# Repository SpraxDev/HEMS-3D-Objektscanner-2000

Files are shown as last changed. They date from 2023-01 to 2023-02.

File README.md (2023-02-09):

# 3D-Objektscanner 2000
Im Rahmen eines Lernfeldes in der Berufsschule haben wir ([@Yannik-Roesser](https://github.com/Yannik-Roesser) und [@SpraxDev](https://github.com/SpraxDev)) den 3D-Objektscanner 2000 entwickelt.

Im Grunde besteht dieser aus einem Drehteller, auf dem sich ein Objekt befindet – Ein *ToF Sensor* misst die Distanz zum Objekt-Messpunkt und speichert diesen ab.

Der Drehteller dreht sich, wodurch wir eine 360°-Ansicht des Objekts erhalten; Der *ToF Sensor* kann in der Höhe verstellt werden, wodurch wir nun über das gesamte Objekt hinweg messen können.

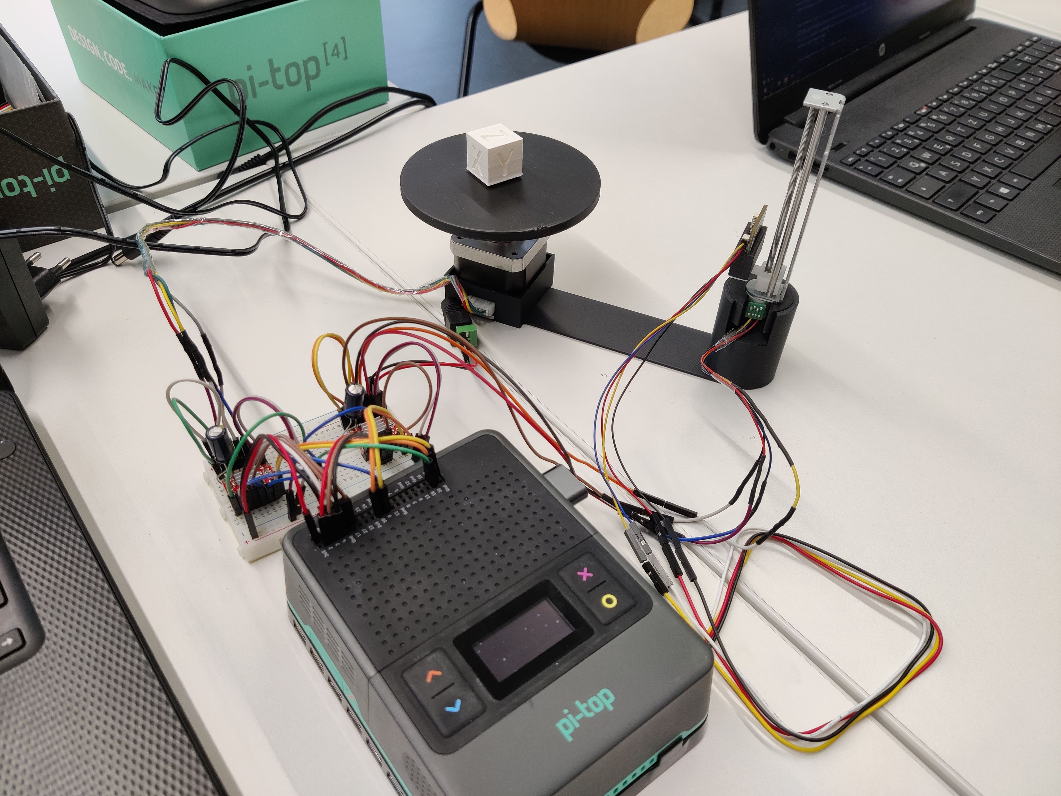
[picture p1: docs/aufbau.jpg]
Bild des Aufbaus mit Raspberry Pi, Drehteller und Distanzsensor

*(Weitere Bilder in [docs/](./docs/))*

## Projektanforderungen
Im Grundlegenden sollten wir folgende Anforderungen erfüllen:
* Verwendung von mindestens vier unterschiedlichen Sensoren oder Aktoren
  * 1x Stepper-Motor (Drehteller)
  * 1x Stepper-Motor mit Linearschlitten (Auf- und Abwärtsbewegung; Für den *ToF Sensor*)
  * 1x ToF Sensor
  * Webinterface (Ein- und Ausgabe; Rendering 3D Modell; Download als STL-Datei)
  * REST-API
* Trennung von Erfassung und Ausgabe der Sensordaten (2 verschiedene Geräte)
  * Erfassung: Python-Script
  * Ausgabe: Webinterface
* Sensorwerte und Eingaben müssen für mindestens 30 Tage gespeichert werden
  * PostgreSQL-Datenbank (Speicherdauer unbegrenzt)
* Fehleingaben des Nutzers müssen entsprechend behandelt werden
  * Validierung der Eingaben
  * Fehlermeldungen (z.B. bei Verbindungsproblemen)
* Klar definiertes Anwendungsgebiet
  * Videospiel-Prototyp günstiger und einfacher herstellen
  * Marketing-Materialien (z.B. für die Produktpräsentation)
  * 3D-Druck (z.B. als Hilfe, wenn ein Objekt als CAD file design werden muss)
  * ...

## Projektstruktur
Das Projekt besteht aus mehrere Software-Komponenten:
* Webinterface-Frontend
* Webinterface-Backend (Webserver + REST-API)
* Python-Script
* FreeCAD
  * Enthält FreeCAD-Projekte, mit Halterungen für die Hardware (zum selber Drucken)
  * Je nach 3D-Druck sind die Maße der Halterungen unter Umständen 1 bis 2 mm zu klein

Funktionen und Aufgaben der Komponenten:
* Das Frontend muss einmalig gebaut werden und kann deployed werden oder vom Backend ausgeliefert werden.
* Das Backend startet einen HTTP-Server, der die REST-API bereitstellt und optional das Frontend ausliefert.
  * Das Backend kann auch auf einem anderen Server laufen, als das Frontend
* Das Python-Script wird auf dem Raspberry Pi ausgeführt, der die meisten Sensoren und Aktoren steuert
  * Das Python-Script kann auch auf einem anderen Server laufen, als das Backend

Die Daten werden in einer PostgreSQL-Datenbank gespeichert.

## Installation
Frontend und Backend benötigen Node.js (getestet mit Version 18) und npm (wird in der Regel mit Node.js mitgeliefert) als package manager.
Für das Python-Skript wird Python 3 benötigt und `pip` als package manager.

### Webinterface-Frontend
1. Im Frontendordner `npm ci` ausführen, um alle notwendigen Pakete zu installieren
2. `npm run build` ausführen, um das Frontend zu bauen
    * Nach der ersten Ausführung, generiert sich eine `config.json` im `config/`-Ordner,
      die angepasst werden kann
3. Das fertige Frontend findet sich im neuen `dist/`-Ordner – Dieses kann (optional) manuell auf ein anderes System deployed werden

### Webinterface-Backend
1. Im Backendordner `npm ci` ausführen, um alle notwendigen Pakete zu installieren
2. `npm run build` ausführen, um das Backend zu bauen
3. Das fertige Backend findet sich im neuen `dist/`-Ordner – Die (production) Abhängigkeiten in `node_modules/` werden zur Ausführung benötigt
4. Zum Starten `npm run start` ausführen
    * Es generiert sich eine `config.json` im `config/`-Ordner, die angepasst werden muss
    * Wurde das Frontend vorab gebaut und die Projekt-Ordnerstruktur nicht verändert, wird dieses
      automatisch gefunden und ausgeliefert

### Python-Script und Hardware
1. Die Hardware, wie in `Verkabelung.fzz` beschrieben, anschließen
2. Die Hardware mit den GPIO-Pins des Raspberry Pi verbinden
    * *ToF Sensor* an den I2C-Bus anschließen
    * Die Motor-Driver-Boards an die entsprechenden Pins aus `scanner-script/scanner_controller.py` (ca. ab Zeile 109 bei `GPIO_motorTeller` und `GPIO_motorVert`)
3. Im Python-Script-Ordner `pip3 install -r requirements.txt` ausführen, um alle notwendigen Pakete zu installieren
    * Es empfiehlt sich vorab ein virtuelles Python-Environment anzulegen
    * Unter Umständen muss `pip` anstelle von `pip3` verwendet werden
4. Skript bei Bedarf konfigurieren
    * `postgres.py` anpassen, um die Datenbankverbindung zu konfigurieren
    * `DISTANCE_BETWEEN_SENSOR_AND_TURN_TABLE_CENTER_MM` in `scanner_controller.py` anpassen, um die Entfernung zwischen dem ToF-Sensor und dem Mittelpunkt des Teller zu konfigurieren
4. `python3 scanner_controller.py` ausführen, um das Script zu starten
    * Unter Umständen muss `python` anstelle von `python3` verwendet werden
5. Das Script wartet nun auf einen Startbefehl über die REST-API

### PostgreSQL Datenbank
Die `/database.sql` enthält die Datenbankstruktur und muss einmalig in die Datenbank eingespielt werden.
Es enthält keine OWNER-Informationen, da diese je nach Umgebung variieren können.

## Unsere Einkaufsliste
Dies sind die Teile, die wir im Rahmen der Projekt-Konzeption verwendet haben.
Ein Breadboard und Kabel sind ebenfalls Notwendig – Die 2 Raspberry Pis haben wir ebenfalls nicht aufgelistet, da diese als Teil der Aufgabenstellung bereits vorhanden waren.

* [Steppermotor mit Linearschlitten](https://smile.amazon.de/dp/B07H4M3KW2/)
  * Hierran befestigen wir unseren *ToF Sensor*
* [NEMA17-04](https://www.reichelt.de/schrittmotor-nema-17-1-8-1-5-a-3-3-v-nema17-04-p269223.html)
  * Nutzen wir für unseren Drehteller (lieber einen stärkeren Motor nehmen, da wir den Teller auch mit Gewicht bewegen wollen)
* 2x [A4988 Schrittmotor-Treiber-Modul](https://www.az-delivery.de/products/a4988-schrittmotor-modul)
  * Damit können wir die beiden Motoren ansteuern
  * [Das Video könnte hilfreich sein](https://www.youtube.com/watch?v=_5H7ibWQgXo)
* [Steckernetzteil 12V 2A](https://www.reichelt.de/steckernetzteil-24-w-12-v-2-a-hnp-24-120l6-p177030.html)
  * Damit können wir den NEMA17-04 bzw. das Treibermodul mit Strom versorgen
* [Kupplung, Ø außen: 5,5 mm, Ø innen: 2,1 mm (DELOCK 65421)](https://www.reichelt.de/kupplung-aussen-5-5-mm-innen-2-1-mm-delock-65421-p127462.html)
  * Darüber verbinden wir das Netzteil mit dem Treibermodul
  * *Hätte auch einfach abgeschnitten und 2 Steckverbindungen draufgelötet, aber lassen wir das beim Schulprojekt mal lieber*
* [Adafruit VL6180X Time of Flight Micro-LIDAR Distance Sensor](https://www.adafruit.com/product/3316)
  * Damit messen wir die Distanz zum Objekt, dass auf dem Drehteller liegt
* 2x [100µF Capacitor (ca. 70 V)](https://www.reichelt.de/elko-radial-100-uf-63-v-105-c-low-esr-aec-q200-rad-fc-100-63-p84621.html)
  * Kommt zur externen Stromversorgung des Motors (möglichst nah am Driver-Board)
    * Details gibts im [Datasheet](https://cdn.shopify.com/s/files/1/1509/1638/files/A4988_Stepper_Motor_Driver_Datenblatt_AZ-Delivery_Vertriebs_GmbH.pdf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)
  * Weniger als 70 V ist sicherlich auch okay, aber keinesfalls unter 40 V würde ich sagen

## Lizenz
Das Projekt ist grundsätzlich unter der MIT-Lizenz veröffentlicht.

Das verwendete Logo im Frontend ist von DinosoftLabs auf Flaticon, lizensiert unter der [Flaticon license](https://www.freepikcompany.com/legal).

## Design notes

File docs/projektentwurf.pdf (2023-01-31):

## Lernfeld 7:

Cyber-physische Systeme ergänzen | Kooperation von Friedrich-List-Schule
| und Heinrich-Emanuel-Merck-Schule
Teammitglieder: Christian Koop, Yannik | in der Ausbildung der IT-Berufe

## Rößer

## Konzept zu [3D-Objektscanner 2000]

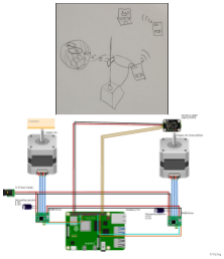
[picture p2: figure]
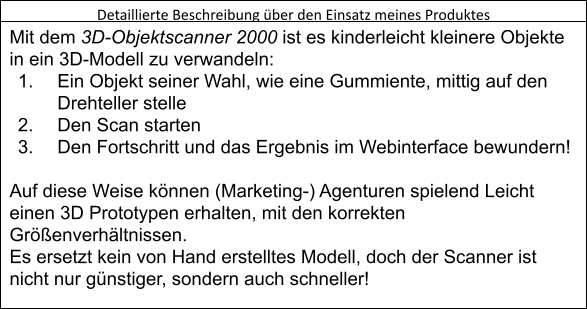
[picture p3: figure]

## Teammitglieder: Christian Koop, Yannik in der Ausbildung der IT-Berufe Rößer

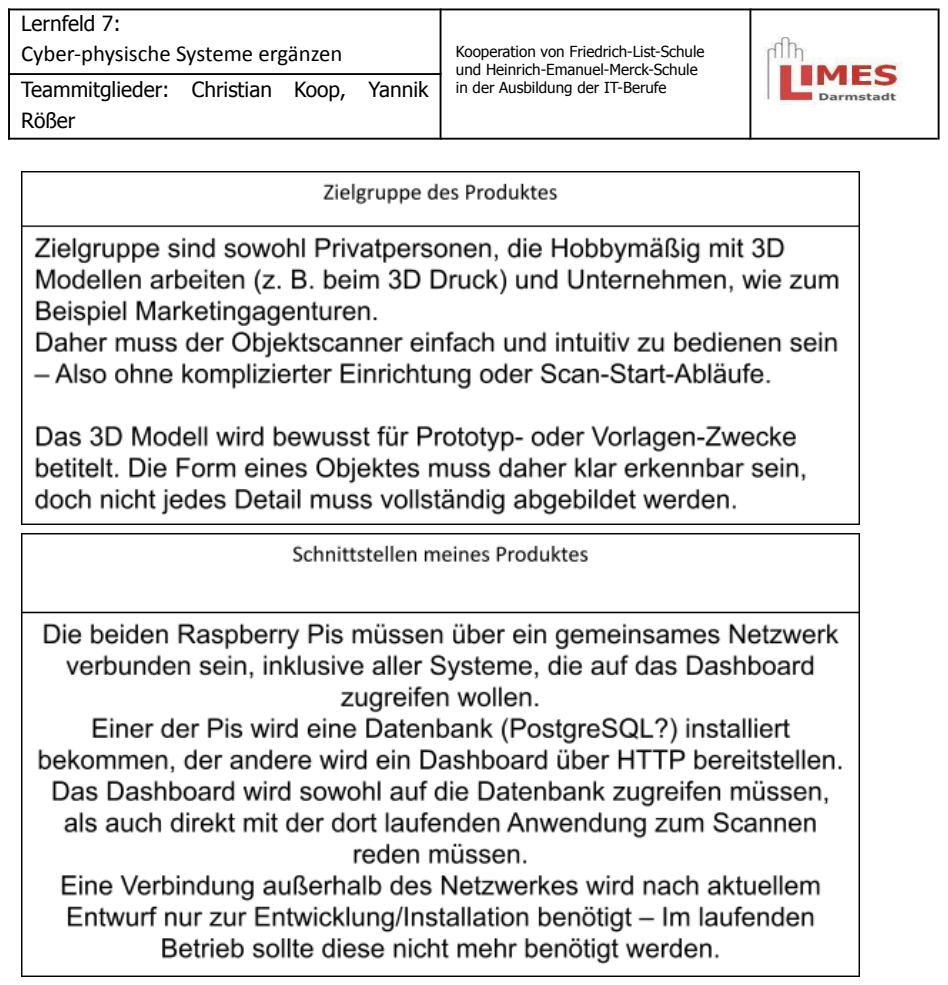
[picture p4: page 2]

und Heinrich-Emanuel-Merck-Schule

## Teammitglieder: Christian Koop, Yannik in der Ausbildung der IT-Berufe Rößer

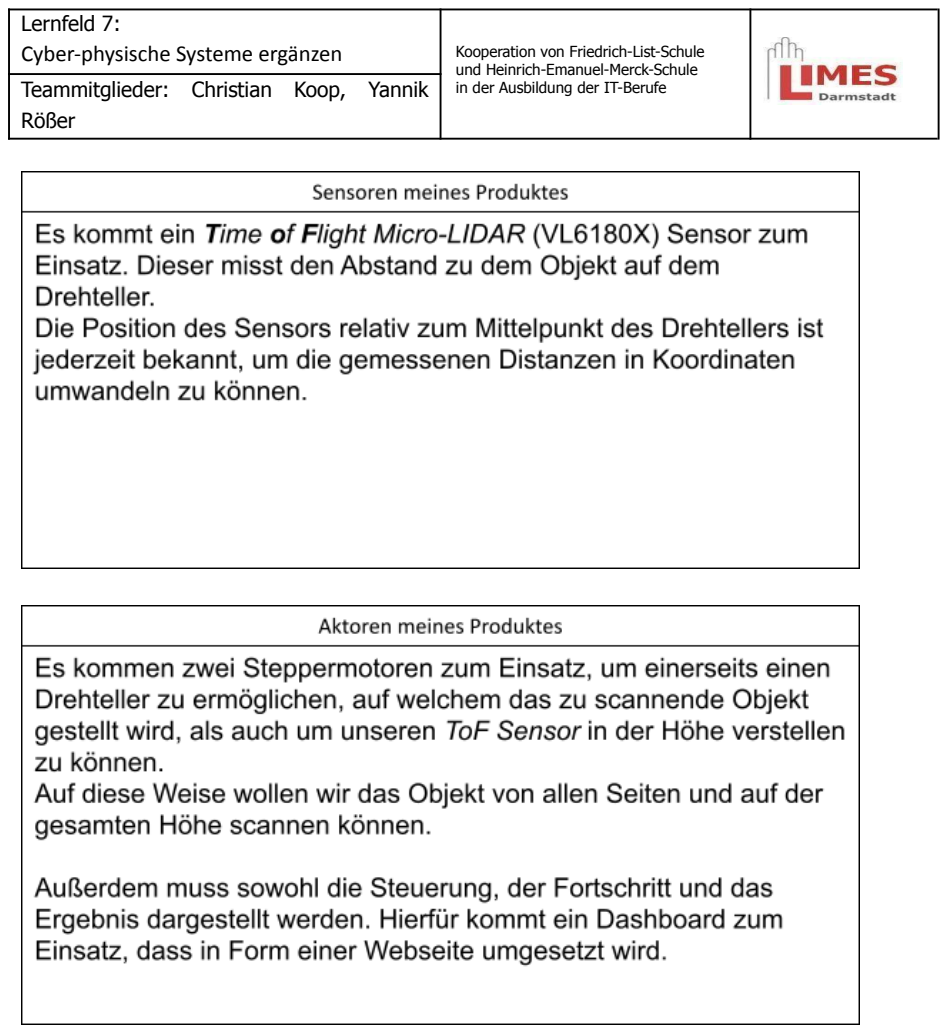
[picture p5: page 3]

und Heinrich-Emanuel-Merck-Schule

## Teammitglieder: Christian Koop, Yannik in der Ausbildung der IT-Berufe Rößer

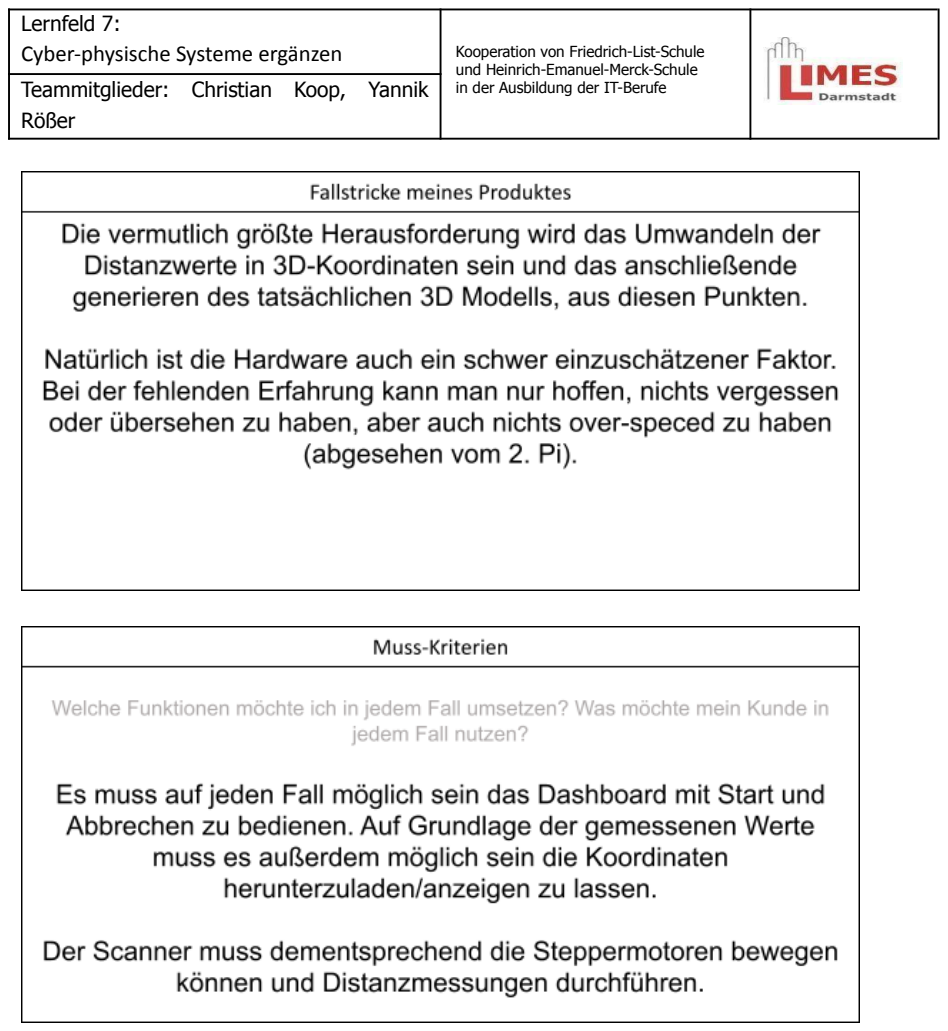
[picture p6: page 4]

und Heinrich-Emanuel-Merck-Schule

## Teammitglieder: Christian Koop, Yannik in der Ausbildung der IT-Berufe Rößer

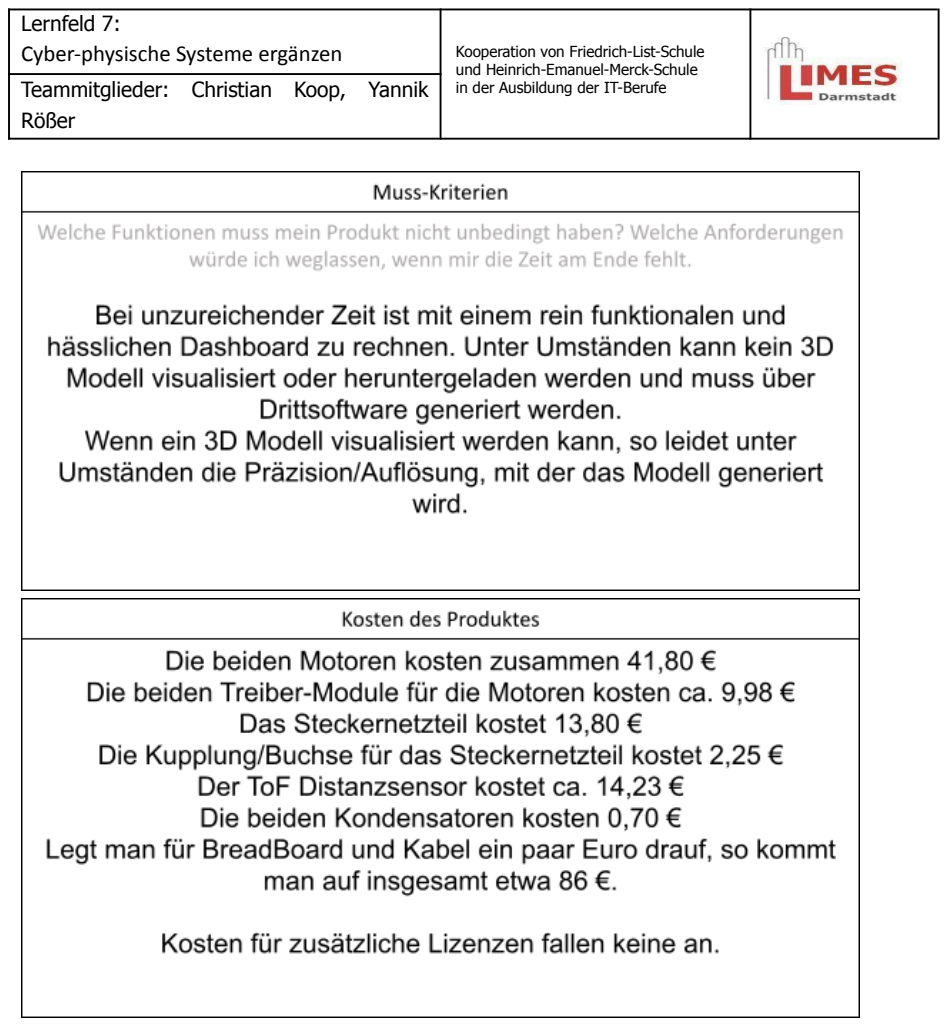
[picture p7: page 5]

und Heinrich-Emanuel-Merck-Schule

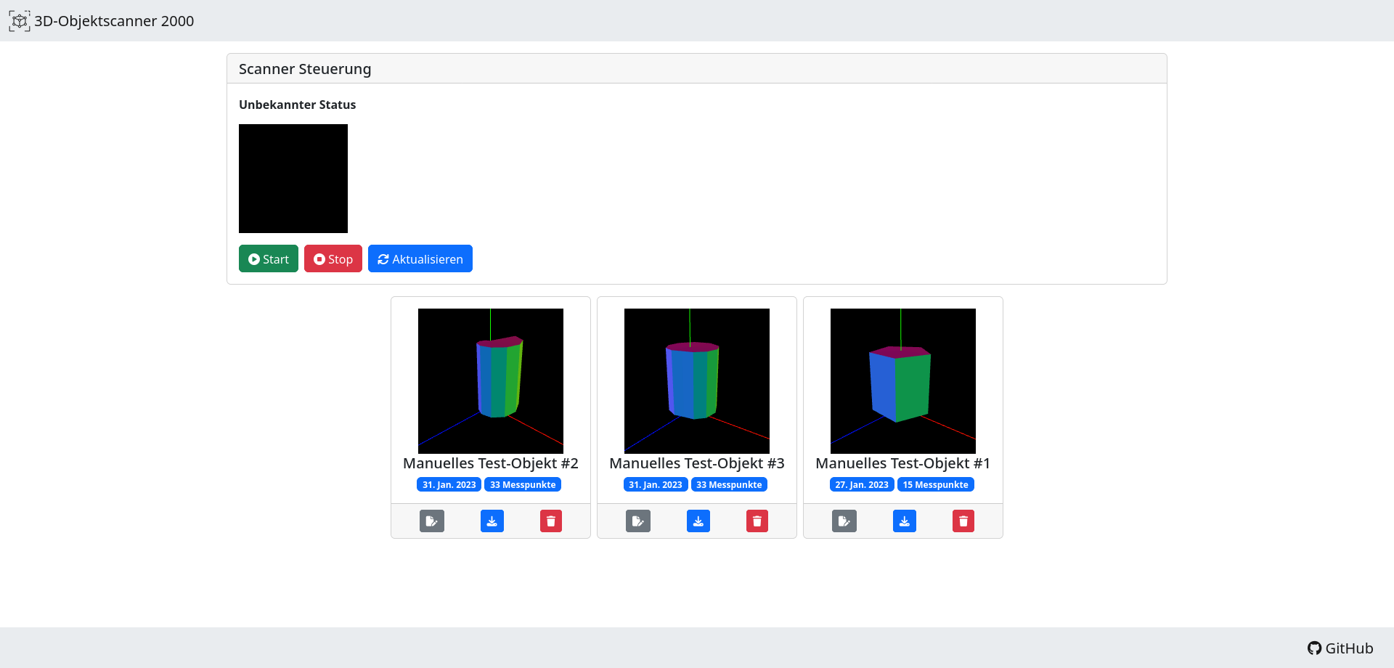
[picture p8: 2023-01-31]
docs/webinterface.png

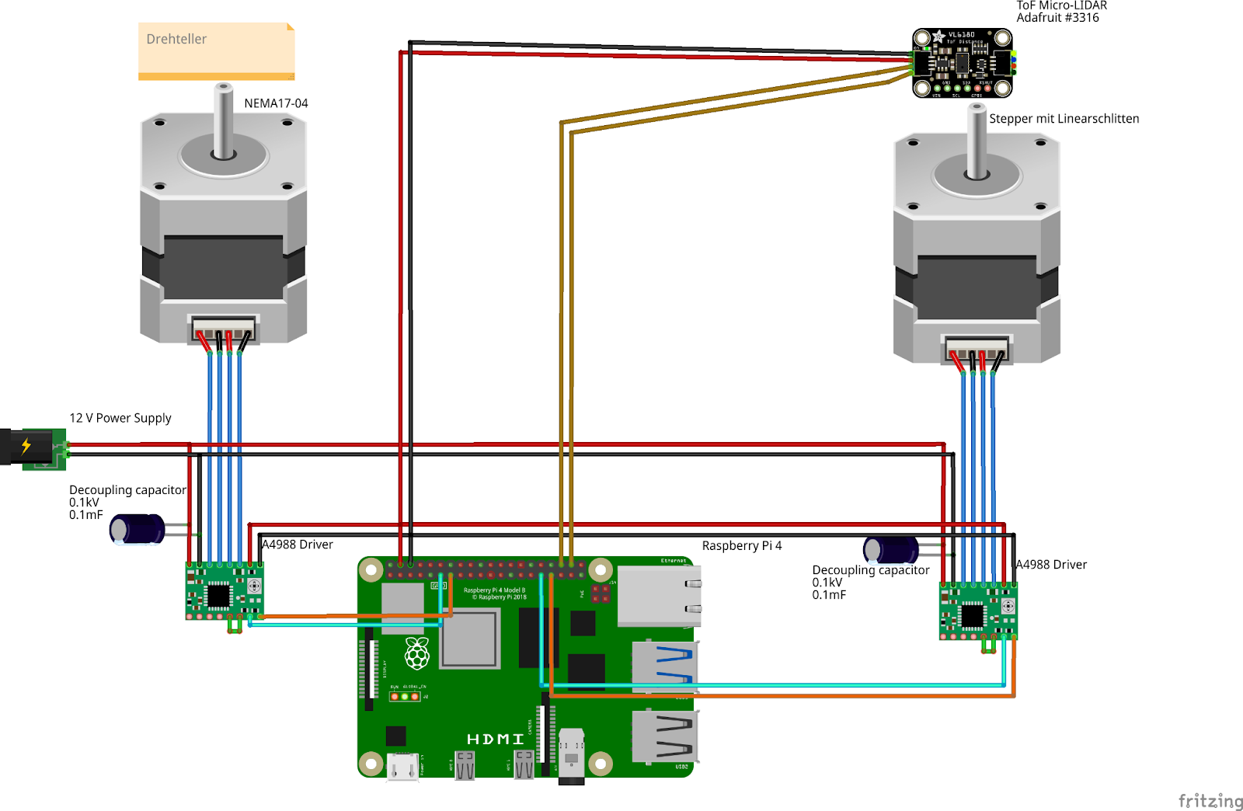
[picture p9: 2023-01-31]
docs/verkabelung.png

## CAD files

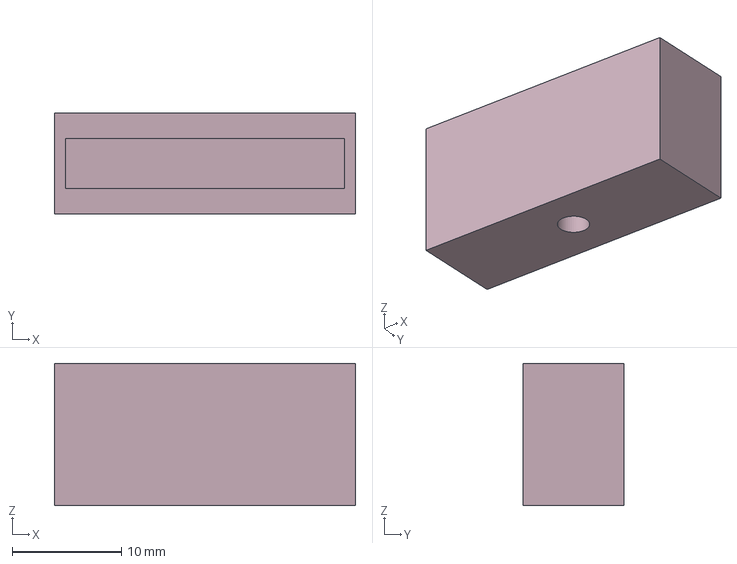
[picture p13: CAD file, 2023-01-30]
FreeCAD/LiDar-Sensor-Mount.FCStd
27.5 x 9.20 x 13.0 mm

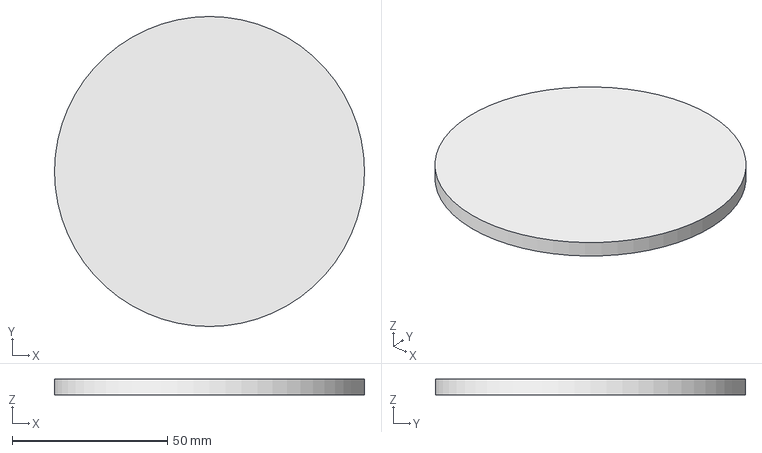
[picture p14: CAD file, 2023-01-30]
FreeCAD/Drehteller.FCStd
100.0 x 100.0 x 5.00 mm

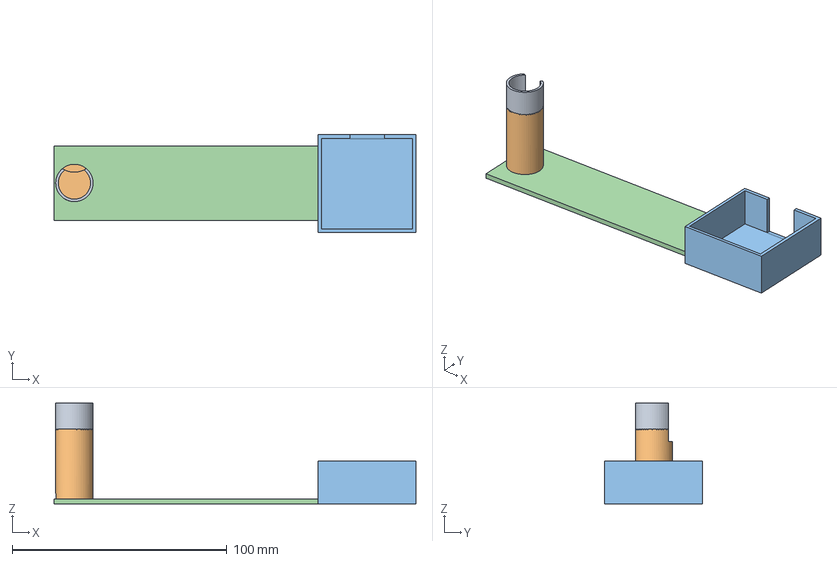
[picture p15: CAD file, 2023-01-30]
FreeCAD/Baseplate.FCStd
168.5 x 45.5 x 47.0 mm
Hülle
Boden

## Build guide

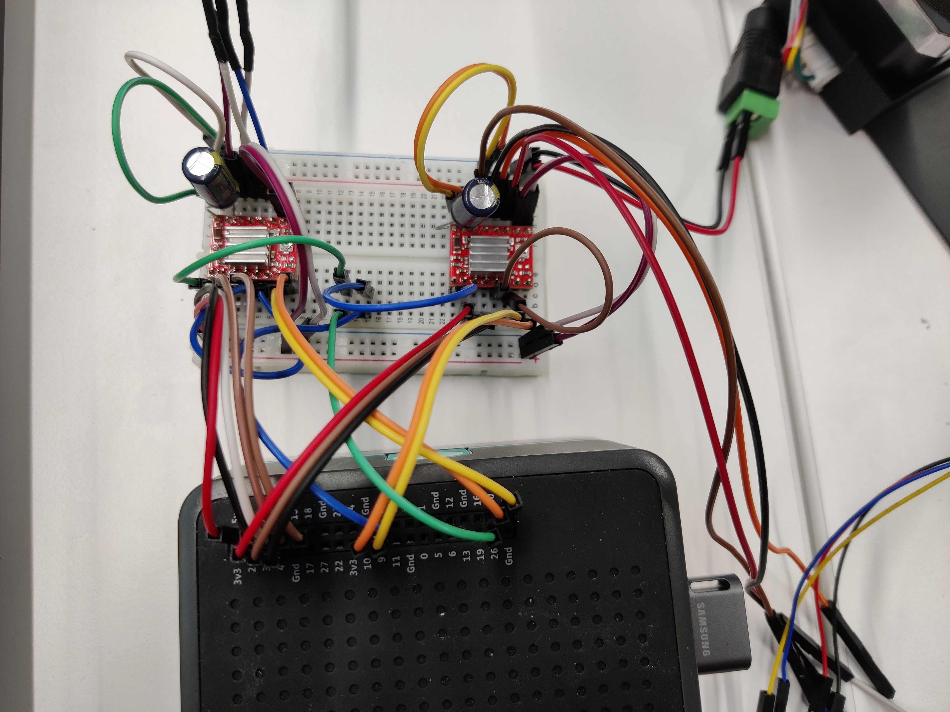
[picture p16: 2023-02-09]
docs/aufbau_3.jpg

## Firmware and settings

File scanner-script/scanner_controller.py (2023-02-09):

from time import sleep
import RPi.GPIO as GPIO
from RpiMotorLib import RpiMotorLib
import signal
import board
import adafruit_vl53l1x
import postgres
import webserver
import scanner_state

FORWARD = True
REVERSE = False

DISTANCE_BETWEEN_SENSOR_AND_TURN_TABLE_CENTER_MM=100

def handler(signum, frame):
    res = input("Interrupt? y/n: ")
    if res == 'y':
        GPIO.output(GPIO_motorTeller.GPIO_driver_enable_pin, GPIO.HIGH)
        GPIO.output(GPIO_motorVert.GPIO_driver_enable_pin, GPIO.HIGH)
        sensor.stop_ranging()
        exit(1)

def sensor_scan():
    sleep(.1)
    if sensor.data_ready:
        measuredDistance = sensor.distance * 10
        normalizedDistance = measuredDistance / DISTANCE_BETWEEN_SENSOR_AND_TURN_TABLE_CENTER_MM
        normalizedDistance = max(0, min(1, normalizedDistance))
        print("Current Scan >> Distance: {} mm (Normalized: {})".format(measuredDistance, normalizedDistance))
        sensor.clear_interrupt()
        return normalizedDistance

class motor():
    def __init__(self, GPIO_direction_pin, GPIO_step_pin, GPIO_pins, motorType, GPIO_driver_enable_pin):
        GPIO.setup(GPIO_driver_enable_pin, GPIO.OUT)
        GPIO.output(GPIO_driver_enable_pin, GPIO.HIGH)
        self.GPIO_direction_pin = GPIO_direction_pin
        self.GPIO_step_pin = GPIO_step_pin
        self.GPIO_pins = GPIO_pins
        self.GPIO_driver_enable_pin = GPIO_driver_enable_pin
        self.motorType = "A4988"

    def setup(self):
        return RpiMotorLib.A4988Nema(self.GPIO_direction_pin, self.GPIO_step_pin, self.GPIO_pins, self.motorType)

def teller_next_step(direction, steps, speed):
    GPIO.output(GPIO_motorTeller.GPIO_driver_enable_pin, GPIO.LOW)
    motorTeller.motor_go(direction, "Full", steps, speed, False, 0.05)
    GPIO.output(GPIO_motorTeller.GPIO_driver_enable_pin, GPIO.HIGH)

def vertical_next_step(direction, steps, speed):
    GPIO.output(GPIO_motorVert.GPIO_driver_enable_pin, GPIO.LOW)
    motorVert.motor_go(direction, "Full", steps, speed, False, 0.05)
    GPIO.output(GPIO_motorVert.GPIO_driver_enable_pin, GPIO.HIGH)


def start_scan():
    scanner_state.state = scanner_state.STATE_RUNNING
    scan_id = postgres.psql_create_object()
    current_scan(scan_id)
    scan_id = -1

def current_scan(scan_id):
    verticalSteps = 0
    while verticalSteps < 3000:
        if scanner_state.state == scanner_state.STATE_SHOULD_STOP:
            break
        tellerSteps = 0
        while tellerSteps < 100:
            if scanner_state.state == scanner_state.STATE_SHOULD_STOP:
                break
            postgres.psql_add_object_measurement(object_id= scan_id, height_index= verticalSteps/60, rotary_table_index= tellerSteps/2, normalized_measured_distance= sensor_scan())
            sensor_scan()
            tellerSteps+=1
            teller_next_step(FORWARD, 2, 0.05)
        verticalSteps +=60
        vertical_next_step(FORWARD, 60, 0.0005)
    scanner_state.state = scanner_state.STATE_STOPPING
    vertical_next_step(REVERSE, verticalSteps, 0.0005)

def loop():
    while True:
        if scanner_state.state == scanner_state.STATE_SHOULD_START:
            sensor.start_ranging()
            start_scan()
        elif scanner_state.state == scanner_state.STATE_STOPPING:
            sensor.stop_ranging()
            scanner_state.state = scanner_state.STATE_READY
        sleep(1)
        


#Setup GPIO
GPIO.setmode(GPIO.BCM)
GPIO.setwarnings(False)

#Setup Interrupt
signal.signal(signal.SIGINT, handler)

# Define Motors and Sensor
GPIO_motorTeller = motor(GPIO_direction_pin=20, GPIO_step_pin=21, GPIO_pins=(14, 15, 18), GPIO_driver_enable_pin=26,motorType="A4988")
GPIO_motorVert = motor(GPIO_direction_pin=10, GPIO_step_pin=9, GPIO_pins=(2, 3, 4), GPIO_driver_enable_pin=25, motorType="A4988")
i2c = board.I2C()
sensor = adafruit_vl53l1x.VL53L1X(i2c)

#Setup Motors and Sensor
motorTeller = GPIO_motorTeller.setup()
motorVert = GPIO_motorVert.setup()
sensor.distance_mode = 1
sensor.timing_budget = 20



#main
webserver.startWebServerInOwnThread()
scanner_state.state = scanner_state.STATE_READY

loop()

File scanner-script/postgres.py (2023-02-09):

import psycopg2
import datetime

conn = psycopg2.connect(
    host="localhost",
    database="objectscanner_2000",
    user="objectscanner_2000",
    password="objectscanner_2000")

def psql_create_object():
    name = "Object@" + str(datetime.datetime.now())

    cur = conn.cursor()
    cur.execute("INSERT INTO objects (name) VALUES ('Objektname') RETURNING id;", ())

    object_id = cur.fetchone()[0]

    conn.commit()
    cur.close()

    return object_id

def psql_add_object_measurement(object_id: int, height_index: int, rotary_table_index: int, normalized_measured_distance: float):
    if height_index < 0:
        raise ValueError("height_index must be greater than 0")
    if rotary_table_index < 0:
        raise ValueError("rotary_table_index must be greater than 0")
    if normalized_measured_distance < 0 or normalized_measured_distance > 1:
        raise ValueError("normalized_measured_distance must be between 0 and 1")

    cur = conn.cursor()
    cur.execute("INSERT INTO object_measurements(object_id, height_index, rotary_table_index, normalized_measured_distance) VALUES(%s, %s, %s, %s);", (object_id, height_index, rotary_table_index, normalized_measured_distance))
    conn.commit()
    cur.close()

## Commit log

2022-12-19 Creates `Verkabelung.fzz` (fritzing project)
    [Verkabelung.fzz]
2023-01-30 Current frontend progress
    Big thanks to @NudelErde for helping me out with in
    `ModelRenderer.ts` - Had trouble rendering the measurement data
2023-01-30 Current backend progress
2023-01-30 Adds FreeCAD files for 3D printing
    [Baseplate.FCStd, Drehteller.FCStd, LiDar-Sensor-Mount.FCStd]
2023-01-30 Frontend: Add rename, export, delete buttons and a lot of notifications
2023-02-04 Fix log message printing cm instead of mm in python script
    [scanner_controller.py]
2023-02-09 Uploads three images of the finished project
    [verkabelung.fzz]
2023-02-09 Minor fixes for the python script
    Last minute changes made before the presentation
    [postgres.py, scanner_controller.py, webserver.py]
2023-02-09 README.md: Put the image a couple paragraphs down
    The image is pretty big and I prefer having the introduction text first
